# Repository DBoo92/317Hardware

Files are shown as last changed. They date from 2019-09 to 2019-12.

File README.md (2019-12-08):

# 317Hardware

## Table of Contents

- [Introduction](#introduction)
- [Bill of Materials](#bill-of-materials)
  * [Parts list](#parts-list)
  * [Custom Parts](#custom-parts)
  * [Tools List](#tools-list)
- [Time Commitment](#time-commitment)
- [PCB/Soldering](#pcbsoldering)
  * [ADS1115 soldering](#ads1115-soldering)
  * [PCB soldering](#pcb-soldering)
  * [Motor soldering](#motor-soldering)
  * [Sensor soldering](#sensor-soldering)
- [Mechanical Assembly](#mechanical-assembly)
  * [ADS1115 risers](#ads1115-risers)
  * [PCB risers](#pcb-risers)
  * [Thread acrylic](#thread-acrylic)
  * [Mount Pi](#mount-pi)
  * [Mount motor](#mount-motor)
  * [Install case fan](#install-case-fan)
  * [Assemble case](#assemble-case)
  * [Plug in connectors](#plug-in-connectors)
  * [Water lines](#water-lines)
  * [Spray nozzle](#spray-nozzle)
- [Power Up](#power-up)
  * [Load OS](#load-os)
  * [Import libraries](#import-libraries)
- [Unit Testing](#unit-testing)
  * [Sensor test](#sensor-test)
  * [Water switch test](#water-switch-test)
  * [Motor test](#motor-test)
  * [Full system test](#full-system-test)
- [Production Testing](#production-testing)
- [Conclusion](#conclusion)

## Introduction

Welcome to my CENG 317 hardware project page. The aim of this project is to create a system for monitoring greenhouse conditions using a Broadcom development platform and various sensors/effectors. Here is a diagram of the proposed systemm:

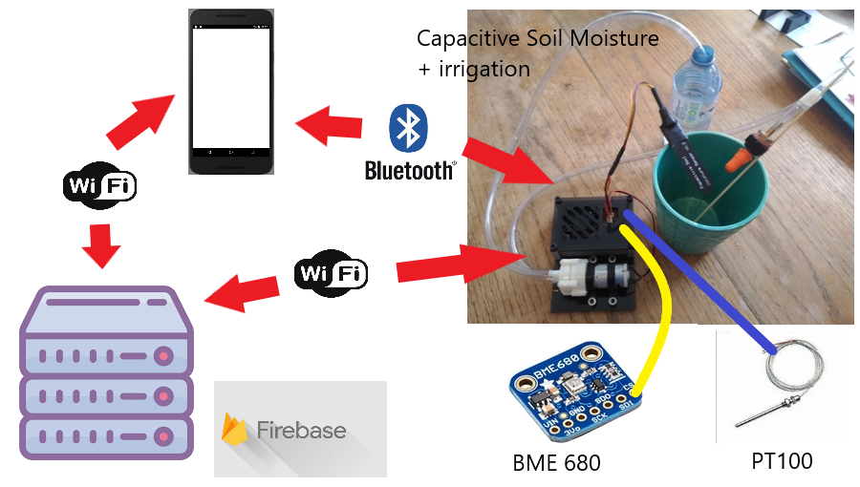
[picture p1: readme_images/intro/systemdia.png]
Systemdiagram


The system consists of a Raspberry Pi which takes readings from various sensors and places them into a Firebase database via WiFi. If these readings are outside of certain ranges/thresholds the device will activate a certain effector to adjust the environment/conditions. All of this data will be viewable from within our app which will connect to the database via WiFi. The app will also be able to control/turn on the various effectors through Bluetooth.

The BME 680 and PT100 sensors are being covered by my group members, Ryan and Aiden respectively.The app is covered in a different course, CENG 319 - [GreenSense App](https://github.com/Aidenbolos/Green-Sense). These build instructions will focus solely on the capacitive soil moisture platform (seen in the system diagram above and the diagram below).

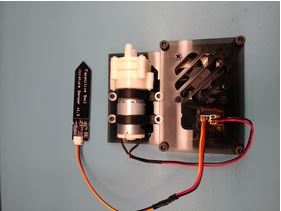
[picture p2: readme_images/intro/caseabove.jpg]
soilmoisture


This project features a capacitive soil moisture sensor for monitoring soil conditions, a pump/irrigation system for watering the plant/soil, and a watering level switch for selecting the amount of water to be dispersed to the plant. 

## Bill of Materials

### Parts List:

| Part/Material | Part Number | Supplier | Qty | Approx. Cost |
|---|---|---|:---:|---:|
| Raspberry Pi 4 starter kit <br> (includes power supply, HMDI, <br> SD card, and card reader) | 99467 | CanaKit (Amazon) | 1 | $134.99 |
| Capacitive Soil Moisture sensor | EK1940 | Gikfun (Amazon) | 1 | $8.48 |
| Mini Diaphragm Pump | EK1856C | Gikfun (Amazon) | 1 | $11.67 |
| ADS1115 (or ADS1015) | 4260474032037 | Universal Solder (Amazon) | 1 | $7.89 |
| 1K ohm resistor | | Electronics store | 3 | $0.30 |
| PN2222A transistor | | Electronics store | 1 | $0.25 |
| IN4001 diode | | Electronics store | 1 | $0.15 |
| 1P3T switch | SMC-549-1 | Sayal Electronics | 1 | $1.50 |
| 2.1mm DC power jack | GAK-1973E-2 | Sayal Electronics | 1 | $0.80 |
| 6v - 12v power supply (2.1mm plug) | | Electronics store | 1 | $9.95 |
| 50mm case fan (with screws) | 8880205 | Princess Auto | 1 | $1.99 |
| 20 pin GPIO header (single row) | | Electronics store | 1 | $0.50 |
| 3 pin Molex connectors (female) | 37-603-5 | Mode Electronics (Sayal Electronics) | 2 | $1.00 |
| 3 pin Molex header (male) | 37-6203-5 | Mode Electronics (Sayal Electronics) | 2 | $1.00 |
| 22 AWG solid wire | | Electronics store | 1 ft | $0.50 |
| 1/8" heatshrink | | Electronics store | 1 ft | $0.40 |
| 63/37 solder (small roll) | 4880-18G | MG Chemicals (Sayal Electronics) | 18g | $3.95 |
| Cone spray nozzle (3/8" thread) | SG-4200TIP-CSK| Valley Industries (Princess Auto) | 1 | $6.49 |
| 1/4" barbed to 3/8" NPT fitting | 903-41161001  | Sioux Chief (Home Depot) | 1 | $3.25 |
| Clear vinyl tube 1/4" ID | | Hardware store | 4 ft | $2.00 |
| M5 x 0.8 x 40mm socket head screw | | Bolts Plus | 4 | $2.80 |
| M3 x 0.5 x 16mm socket head screw | | Bolts Plus | 4 | $1.60 |
| M2.5 x 0.45 x 10mm button head screw  | | Bolts Plus | 4 | $1.20 |
| M3 x 0.5 nuts | | Bolts Plus | 4 | $0.40 |
| M2.5 x 0.45 nuts | | Bolts Plus | 2 | $0.10 |
| M3 washers | | Bolts Plus | 20 | $1.00 |
| 10mm PCB risers (with nuts/screws) | | Hardware store | 4 | $0.80 |
| 12" x 12" x 1/8" acrylic | | Hardware store | 1 | $10.00 |

### Custom Parts:

| Part | Source file | Approx. Cost |
|---|---|---:|
| PCB manufacturing | [PCB gerber files](https://github.com/DBoo92/317Hardware/blob/master/electronics/SoilMoisture_Gerber.zip) | $20.00 |
| 3D printing | [3D .stl file](https://github.com/DBoo92/317Hardware/blob/master/mechanical/ProjectBoxMiddleRPI.stl)| $15.00 |
| Acrylic laser cutting | [Acrylic Top cut file](https://github.com/DBoo92/317Hardware/blob/master/mechanical/CaseTop.cdr) <br> [Acrylic Bottom cut file](https://github.com/DBoo92/317Hardware/blob/master/mechanical/CaseBottom.cdr) | $10.00 |

> Tip 1: If you haven't already ordered/received the custom parts above, please find a PCB manufacturer, 3D print shop, and a laser cutting shop. Use the source files above and have these parts made before beginning your project.

### Tools List:

| Tool                       | 
|----------------------------|
| HDMI monitor/TV            |
| USB mouse and keyboard     |
| Soldering iron             |
| Wire strippers             |
| Diagonal cutting pliers    |
| Heat gun (or blow dryer)   |
| Digital Multimeter         |
| M5 x 0.8 tap + handle      |
| Small square file          |
| 4mm allen key              |
| 2.5mm allen key            |
| 1.5mm allen key            |
| Philips #2 screwdriver     |
| X-Acto knife               |

## Time Commitment

Time required to complete this project is approximately: **12 - 16 hours** (continuous work), or 2 work days. This varies depending on skill level.

It is best to approach this project with mild/moderate experience in electronics and circuits, tools and assembly, and computers. However, my aim is to make this guide thorough enough for people of all experience levels.

## PCB/Soldering

Follow the steps below to assemble/solder your PCB.

> Hint: If you do not have prior soldering experience, I recommended reading [this](https://www.makerspaces.com/how-to-solder/) website and watching their demonstration video.

Before beginning please ensure you have an adequate workspace, the appropriate tools, and that everything is clean and tidy. The appropriate safety equipment is outlined in the website above.

### ADS1115 soldering

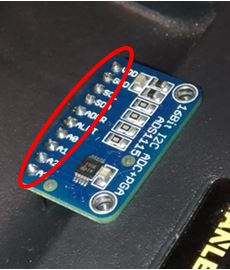
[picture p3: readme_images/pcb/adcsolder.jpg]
ADSsolder Fig 4.1: ADS1115 solder points


Place the 10 pin header through the ADS1115 with the short side of pins going through the holes. Ensure that the pins are at a 90 degree angle with the circuit coard. Solder each pin as circled in red above. Allow time to cool between each solder joint.

### PCB soldering

#### 1. Vias

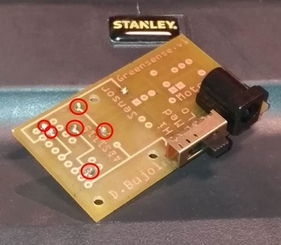
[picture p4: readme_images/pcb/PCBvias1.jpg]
PCBvias1 Fig 4.2: Via solder points (top)
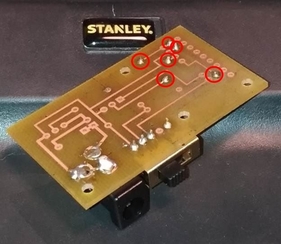
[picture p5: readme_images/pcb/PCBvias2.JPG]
PCBvias2 Fig. 4.3: Via solder points (bottom)
 

Begin by cutting six 2" lengths of your solid core wire and stripping them completely. Place a piece of wire through one of the holes circled in red and solder one side of it. Once the solder joint has cooled, flip the PCB over and solder the other side of the same wire. Using the diagonal cutters, carefully cut off the excess wire on either side down at the tip of the solder joint. Repeat this process for the other 5 holes circled in red.

#### 2. DC Jack and 1P3T Switch

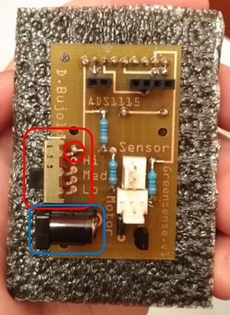
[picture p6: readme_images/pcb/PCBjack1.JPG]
PCBjack1 Fig 4.4: Jack and switch placement
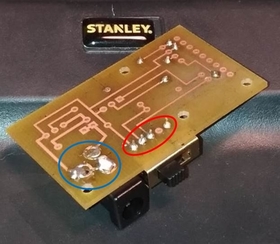
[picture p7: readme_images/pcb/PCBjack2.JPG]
PCBjack2 Fig 4.5: Jack and switch solder points
 

Place the DC jack (first image circled in blue) into its mounting holes on the PCB. Ensure that the jack is sitting on top of the board, facing out the side, and its pins/tabs stick out the bottom. Bend the 3 tabs down towards the PCB to help hold the jack in place and to allow for a better solder connection. Solder each tab individually on the bottom of the board (second image circled in clue). Allow time to cool in between each pin (to avoid melting the plastic).

Place the 1P3T switch (first image circled in red) into its mounting holes on the PCB. Ensure that the switch is sitting on top of the board, facing out the side, and its pins stick out the bottom. Bend the pins slightly to help hold the switch in place. Solder each pin individually on the bottom of the board (second image circled in red). After this is done solder just the far left hand pin from the top as well (first image interior red circle). One hole will remain empty as seen in the second image.

#### 3. Resistors

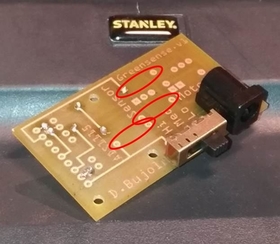
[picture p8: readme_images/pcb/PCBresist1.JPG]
PCBresist1 Fig 4.6: Resistor holes
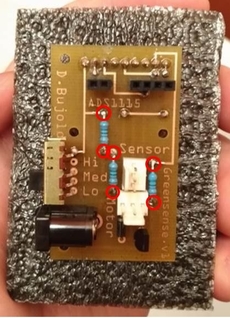
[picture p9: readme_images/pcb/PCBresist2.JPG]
PCBresist2 Fig 4.7: Resistor solder points (top)
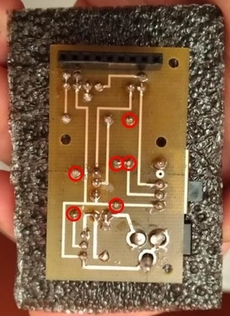
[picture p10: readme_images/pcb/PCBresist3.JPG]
PCBresist3 Fig 4.8: Resistor solder points (bottom)
  

Bend the legs on your 1k ohm resistors so each resistor aligns with a pair of holes (first image circled in red). Place the first resistor into its mounting holes from the top of the board and bend the legs from underneath to hold it in place. Solder both the top and bottom holes (second and third image circled in red). Allow time to cool between solder joints to prevent overheating the resistor. Do this for the other 2 resistors.

#### 4. Diode

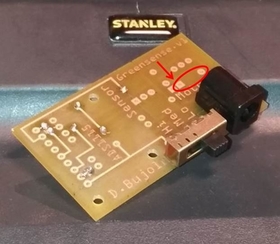
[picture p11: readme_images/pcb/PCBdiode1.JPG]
PCBdiode1 Fig 4.9: Diode holes
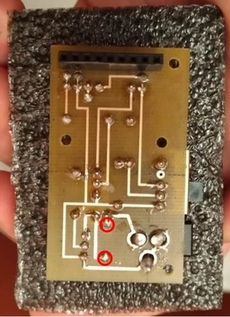
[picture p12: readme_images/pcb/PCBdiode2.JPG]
PCBdiode2 Fig 4.10: Diode solder points (bottom)
 

Bend the legs on your diode so it aligns with its pair of holes (first image circled in red). 

> Tip 2: The silver line on your diode MUST face the square pad on the board (red arrow pointing to it).

Place the diode into its mounting holes from the top of the board and bend the legs from underneath to hold it in place. Solder the diode from underneath the board. Allow time to cool between solder joints to prevent damaging the diode.

#### 5. Transistor

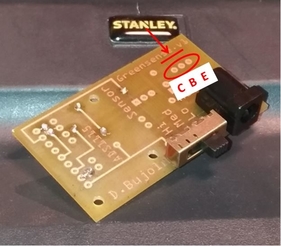
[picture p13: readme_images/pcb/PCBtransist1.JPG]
PCBtransist1 Fig 4.11: Transistor holes
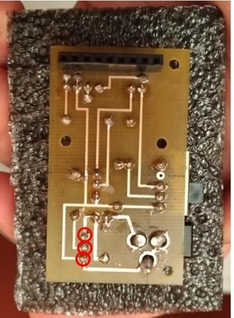
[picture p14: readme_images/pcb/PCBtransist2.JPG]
PCBtransist2 Fig 4.12: Transistor solder points (bottom)
 

Place the transistor into its mounting holes from the top of the board (first image circled in red).

> Tip 3: The flat side on the transistor body MUST face the flat red line in the diagram. However, if you are using a different transistor/package please refer to its data sheet to determine its orientation (collector, base, and emitter are labelled in the diagram).

Bend the pins on the transistor from underneath to help hold it in place. Solder the transistor pins from underneath the board (second image circled in red). It is very important you allow time to cool between each solder joint as transistors are very sensistive to heat.

#### 6. Molex Connectors

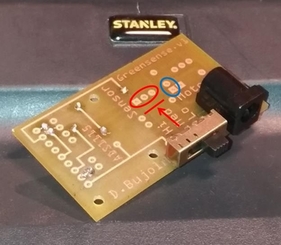
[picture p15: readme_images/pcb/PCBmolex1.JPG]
PCBmolex1 Fig 4.13: Molex holes
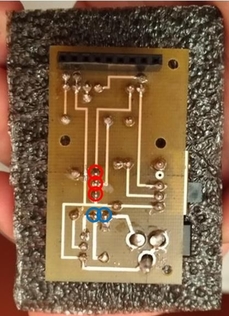
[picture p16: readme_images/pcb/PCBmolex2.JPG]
PCBmolex2 Fig 4.14: Molex solder points (bottom)
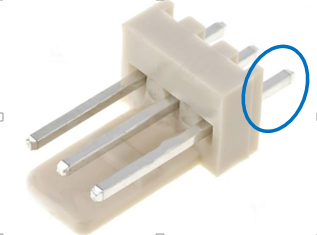
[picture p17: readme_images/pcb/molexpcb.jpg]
PCBmolex3 Fig 4.15: Unused molex pin
  

Place the soil sensor molex connector (circled in red) into its mounting holes from the top of the board.

> Tip 4: The plastic "tab" on the molex connector should face the flat red line in the diagram.

Bend the pins from underneath to hold it in place. Solder each pin from underneath the board (second image circled in red).

For the motor molex connector, cut off or bend flat the bottom pin (third image circled in blue) as it will interfere with mounting and is unused. Place the connector into its mounting holes from the top of the board (first image circled in blue). Solder the two pins from underneath the board (second image circled in blue).

#### 7. ADC and Pi Headers

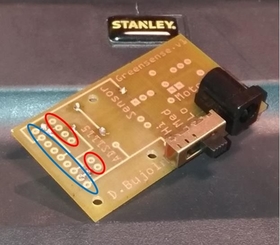
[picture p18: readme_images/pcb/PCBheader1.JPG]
PCBheader1 Fig 4.16: Header holes
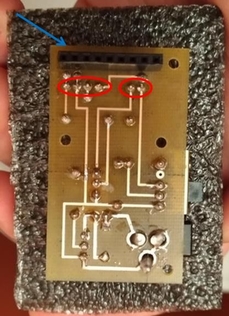
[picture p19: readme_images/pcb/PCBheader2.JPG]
PCBheader2 Fig 4.17: Header solder points (bottom)
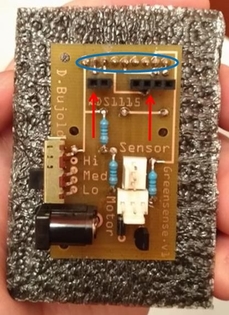
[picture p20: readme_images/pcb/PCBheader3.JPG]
PCBheader3 Fig 4.18: Header solder points (top)
  

If you haven't already, now is the time to cut your headers to size. You will need one 2 pin, one 4 pin, and one 9 pin header. Carefully use the X-Acto knife to cut your headers to the desired size.

Push the 4 pin header onto the Vcc, Gnd, SDA, and SCL pins of the ADS1115. Push the 2 pin header onto the A0 and A1 pins of the ADS1115. Place the headers into their mounting holes from the top of the PCB (first image circled in red) and ensure that the pins stick out the bottom. Flip the PCB over so it is now resting on the ADS1115. Prop up the PCB so it is parallel and square with the ADS1115. Solder the the header pins on the bottom side of the board (second image circled in red).

Push the 9 pin header onto your Raspberry Pi so it sits on pins 1, 3, 5, 7, 9, 11, 13, 15, and 17. Now place the entire PCB (bottom down) onto the 9 pin header (the pins should stick out the top of the PCB - first image circled in blue). Prop up the PCB so it is parallel and square with the Raspberry Pi. Solder the two outermost pins from the top side of the board (third image circled in blue). Now remove the PCB from the Pi with the 9 pin header attached. Finish soldering the other 7 pins from the top side of the board.

#### 8. PCB notch

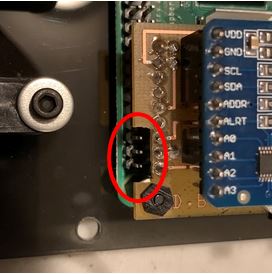
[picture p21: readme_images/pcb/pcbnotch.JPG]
PCBnotch Fig 5.11: Notch for fan power


Use the small square file to cut a notch in the PCB beside the first 3 header pins. Copy the notch in the image above. This will allow us access to the Pi's 5v and Gnd to plug in the case fan.

Now that you have completed the PCB, it is advised to run a couple quick tests:

> Test 1: It is recommended to do continuity tests on side-by-side solder joints or any connections that look close to each other/touching. This is a precaution to help ensure there are no shorts between solder joints.

> Test 2: Use a jumper wire to connect Vcc and Gnd together on the PCB sensor circuit (connect the pins in the header). Then, using a DMM set to ohms, measure resistance between Gnd and A0 on your ADC. You should see a reading between a few hundred thousand ohms and a few million ohms. If you see this reading it indicates your sensor circuit is wired correctly.

### Motor soldering

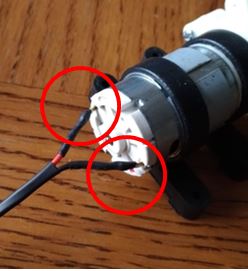
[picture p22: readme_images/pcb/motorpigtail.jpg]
motorsolder Fig 4.19: Motor terminal wires


Cut two pieces of 22 AWG solid wire approximately 8" long and strip 1/4" off each end. Wrap the end of one wire onto one of the motor terminals. Solder this connection. Cut off a 2" piece of heatshrink and slide it down the wire and over the connection. Use the heat gun to heat up the tubing and shrink it. Repeat this process for the second wire and the second motor terminal.

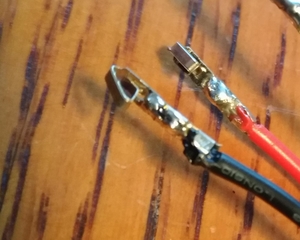
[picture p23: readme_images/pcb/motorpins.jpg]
motorwires Fig 4.20: Motor wires molex pins
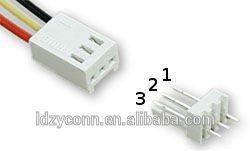
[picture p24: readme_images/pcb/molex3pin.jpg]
motormolex Fig 4.21: Molex pin numbers
 

Using the wire strippers crimp a molex pin onto the open end of each motor wire (shown in the first image). Apply a small amount of solder to the crimp connection to strengthen it. Once the solder has cooled, insert the pins into holes 1 and 2 as labelled in the second picture (doesn't matter which pin goes in which hole).

### Sensor soldering

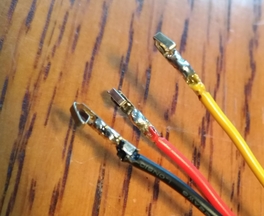
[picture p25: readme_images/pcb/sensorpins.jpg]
sensorwires Fig 4.22: Soil sensor molex pins
 sensormolex Fig 4.23: Molex pin numbers

Cut the stock connector off the soil sensor using the diagonal cutters. Make your cut close to the existing connector so the wires stay long. Strip about 1/4" off the end of each wire. Crimp a molex pin on the open end of each wire (shown in first image) using the wire strippers. Apply a small amount of solder to the crimp connection to strengthen it. Once the solder has cooled, insert the Aout pin into hole 1, Vcc pin into hole 2, and Gnd pin into hole 3 (as labelled in the second picture).

> Tip 5: Make sure the pins go into the appropriate connector hole otherwise it may damage the sensor/circuit.

You are now ready for mechanical assembly.

## Mechanical Assembly

### ADS1115 risers

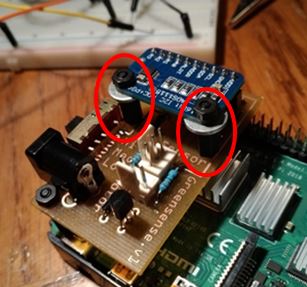
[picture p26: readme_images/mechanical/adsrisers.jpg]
ADSrisers Fig 5.1: ADS1115 risers


Start by inserting a 10mm riser in each mounting hole of the ADS1115 with a 3mm washer underneath it (as shown in the picture). Fasten them by threading a nut on the end of the riser and tightening it. Then from the bottom side of the PCB thread a screw into the riser through the 2 mounting holes and tighten them. Careful not to overtighten anything as the risers are only plastic.

### PCB risers

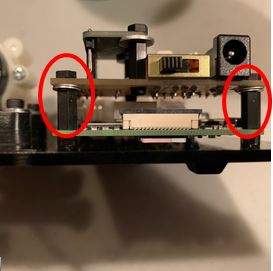
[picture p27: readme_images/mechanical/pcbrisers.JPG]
PCBrisers Fig 5.2: PCB risers


Next insert a 10mm riser into each outer mounting hole on the PCB with a 3mm washer underneath it (as shown in the picture). Fastern them by threading a nut onto the end of the riser and tightening it. Careful not to overtighten as the risers are only plastic.

Now that the ADC is mounted to the PCB and the PCB has its own risers; you are ready to install it onto the Raspberry Pi. Place the PCB onto the Raspberry Pi by lining up the 9 pin header with pins 1, 3, 5, 7, 9, 11, 13, 15, and 17 on the Pi. Press straight down gently on the header to fully seat the PCB onto the Pi.

### Thread acrylic

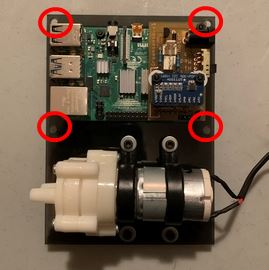
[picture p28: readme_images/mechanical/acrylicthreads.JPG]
acrylicthreads Fig 5.3: Acrylic holes to tap


Before mounting anything to the bottom layer of acrylic, use the M5 x 0.8 tap + handle to tap/thread these 4 holes (outlined in red). 

> Hint: If you haven't used a tap before, follow the instructions on [this](https://disher.com/2016/11/08/whats-tap-hand-taps-beginners/) website.

### Mount Pi

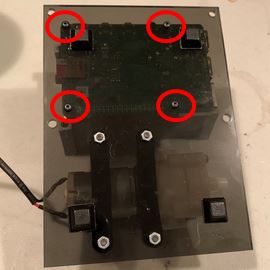
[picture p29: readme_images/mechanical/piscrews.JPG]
Piscrews Fig 5.4: Pi mounting screws
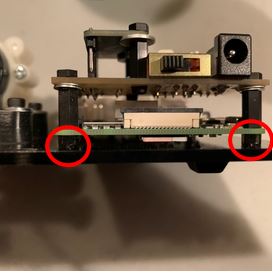
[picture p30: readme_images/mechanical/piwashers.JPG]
Piwashers Fig 5.5: Pi spacers/washers
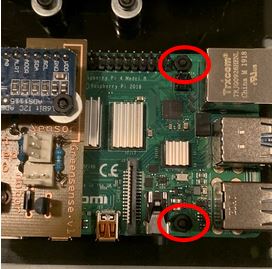
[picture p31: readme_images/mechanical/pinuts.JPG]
Pinuts Fig 5.6: Pi mounting nuts
  

Place an M2.5 x 10mm screw through each of the Pi mounting holes in the acrylic (first image circled in red). Lie the acrylic bottom down with the bolt heads against the table (the bolt threads should be facing upward). Place three 3mm washers onto each bolt on top of the acrylic (similar to the second image). Then line up the Pi over the bolts and lower it on to them (audio/video ports should face outside edge). Thread a M2.5 nut onto the two bolts closest to the ethernet/USB ports and tighten them (third image). Carefully prop the unit up on its side, ensuring the other 2 mounting bolts stay in their holes (as they are not threaded in yet). Use the 1.5mm allen key to tighten up the other 2 mounting bolts from underneath the acrylic (don't overtighten as they are threading into the plastic risers).

### Mount motor

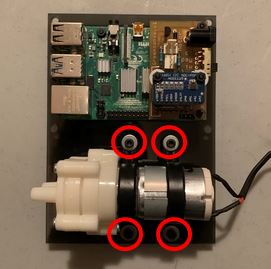
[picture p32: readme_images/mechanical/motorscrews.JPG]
motorscrews Fig 5.7: Motor mounting screws
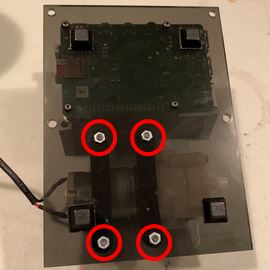
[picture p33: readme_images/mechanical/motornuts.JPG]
motornuts Fig 5.8: Motor mounting nuts
 

Install the included rubber mounts onto the motor body. Place the motor onto the acrylic base. Insert a M3 x 0.5 x 16mm screw with a 3mm washer into each mounting hole (first image circled in red). Then thread a nut onto the bottom of each screw from underneath (second image circled in red). Hold the nut with you fingers while using the 2.5mm allen key to tighten them. The motor mounts are only rubber so do not overtighten/compress the rubber.

### Install case fan

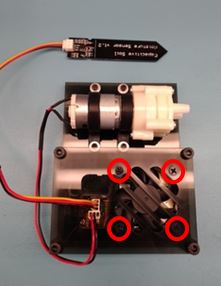
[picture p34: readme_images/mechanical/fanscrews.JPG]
fanscrews Fig 5.9: Case fan screws


Place the fan against acrylic top cover with the "cage" part of the fan facing down (this will ensure air is pulled in). Then use the Philips #2 screwdriver thread the fan screws into the fan (circled in red). Lightly tighten the screws but do not overtighten as the acrylic may crack.

### Assemble case

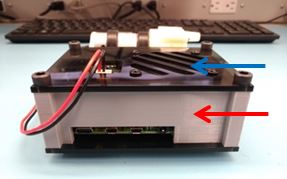
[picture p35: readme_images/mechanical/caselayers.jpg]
caselayers Fig 5.10: Layers of the case
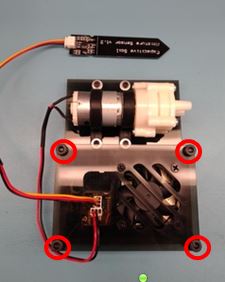
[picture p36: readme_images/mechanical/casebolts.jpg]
casebolts Fig 5.12: Case fastening bolts
 PCBnotch Fig 5.11: Notch for fan power 

Assemble the case by fitting the 3D printed middle section (first image red arrow) over the Pi and onto the acrylic base. Then plug the fan connector into 5v and Ground on the Pi header (where the notch was cut earlier - second image circled in red). Now place the acrylic top (first image blue arrow) onto the 3D printed middle section. Finally, insert the four M5 x 0.8 x 40mm bolts through all three layers and thread them into the bottom layer (third image circled in red). Tighten these bolts with the 4mm allen key (careful not to overtighten).

### Plug in connectors

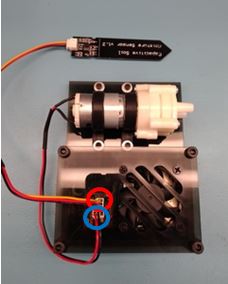
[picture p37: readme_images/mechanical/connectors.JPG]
connectors Fig 5.13: Molex plug in location


Now that the case is assembled we can add the sensor and effector. Plug the 3 pin soil sensor into the center connector on the PCB (circled in red). Then plug the motor connector into the remaining connector on the PCB (circled in blue).

### Water lines

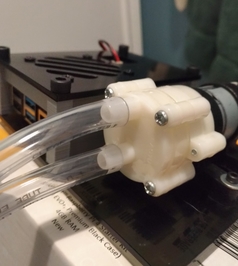
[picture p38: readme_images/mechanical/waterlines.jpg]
waterlines Fig 5.14: Water line attachment


Using the diagonal cutters, cut the clear vinyl tubing into 2 equal length pieces (around 2 ft each). Push the end of a tube onto each water pump barb as shown in the image above.

### Spray nozzle

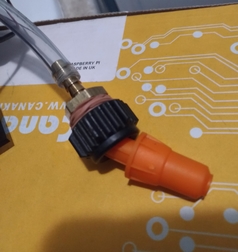
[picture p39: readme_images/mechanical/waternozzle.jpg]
waternozzle Fig 5.15: Spray nozzle setup


Thread the 1/4" barb to 3/8" NPT brass fitting into the spray nozzle threads. Tighten these together firmly to prevent leaks. See above image for reference.

Look on the face of the water pump (where the tubes connect) and note which tube is labelled "IN" and which is "OUT". Then push the barbed end of the nozzle into the open end of the "OUT" tube (as shown in the image above).

You are now ready to power up.

## Power Up

> Tip 6: If you haven't already, please complete the 2 tests listed at the bottom of the PCB soldering section. These will help ensure that no damage is done to your Pi during initial power up.

### Load OS

1. Unfortunately the OS file is too large to post on Github. However, the link below will take you to the Raspberry Pi download page where you can get it. There you can download the OS as either a torrent or a zip file. For this project it is recommended to download the full "Raspbian Buster with desktop and recommended software". You will need at least an 8GB SD card for this.

[Download Raspbian OS](https://www.raspberrypi.org/downloads/raspbian/)

2. Once downloaded, follow the link below for instructions on flashing the OS onto your SD card.

[Install Raspbian OS](https://www.raspberrypi.org/documentation/installation/installing-images/README.md)

3. Finally, follow the link below for help with the intital power up/configuration setup:

[Configure Raspbian](https://projects.raspberrypi.org/en/projects/raspberry-pi-setting-up/4)

4. The Pi starter kit comes with an HDMI cable, so for your initial tests you will be connecting it to an HDMI monitor. However, in the future you are recommended to download VNC Viewer to connect remotely via WiFi or ethernet.

[Download VNC Viewer](https://www.realvnc.com/en/connect/download/viewer/)

5. Use the guide below to help you setup/use VNC Viewer and connect to your Pi.

[Setup VNC Viewer](https://magpi.raspberrypi.org/articles/vnc-raspberry-pi)

### Import libraries

Now that the Pi is setup and running you will need to import this library to access the readings from the ADS1115.

Open the terminal and run the following commands one at a time. You may see some text appear between each command, allow it to finish before inputting the next command.

```sh
sudo apt-get update
sudo apt-get install build-essential python-dev python-smbus git
cd ~
git clone https://github.com/adafruit/Adafruit_Python_ADS1x15.git
cd Adafruit_Python_ADS1x15
sudo python setup.py install
```

You now have the necessary libraries and some sample code to work with.

## Unit Testing

I suggest testing the sensor and watering level switch first without the motor functionality. This way it is easier to troubleshoot if you run into problems.

### Sensor test

Now that everything is assembled and the software is installed you are ready to test the sensor. The sensor should be connected to the PCB at this point and you should have a glass of water nearby to simulate soil moisture.

Power up your Pi and open a terminal session. Enter the following command to navigate to the Adafruit example code you downloaded earlier:

```sh
cd ~/Adafruit_Python_ADS1x15/examples
```

Now that you are in the examples folder, run this command:

```sh
nano simpletest.py
```

> Tip 7: Use CTRL-c to stop the program when you are done.

The program should start up in the terminal. You will see the readings of the 4 ADS1115 channels displayed in a table. See the picture below as an example:

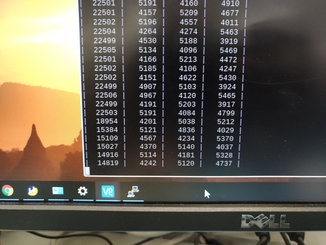
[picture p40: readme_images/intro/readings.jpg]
readings Fig 7.1: Test readings


The soil sensor values are shown in the first column. In dry air the sensor should read around 24,000. Test the senor by placing it into the glass of water. You should see these readings drop down below 15,000. Repeat this a few times to ensure things are working well.

### Water switch test

The watering level switch values are shown in the second column. Test the switch by flipping it between its 3 positions. You should see the readings change between low (under 1000), medium (around 15000), and high (over 24000). Again, repeat this a few times for verification. You may stop the program now.

Once you have confirmed that these two are working correctly you may now test the motor.

### Motor test

The motor should be connected to the PCB and the water hoses connected to the motor. Plug the 6 - 12v power supply into the wall and plug the 2.1mm plug into the DC jack on the PCB. Place the "IN" hose into a cup of water and the "OUT" hose into an empty cup. Unscrew and remove the top cover from the project case and disconnect the fan for now. Using a wire with alligator clips on either end, clip one end to the Pi 5v output (where the fan was connected). Clip the other end onto the middle leg (Base) of the transistor (careful not to touch the other legs). The motor/pump should now turn on. Check to make sure the pump is working correctly and you are getting a steady mist/stream out of the spray nozzle. Once you are done - remove the alligator clips, replace the fan connector, and reinstall the top cover.

If all three components are working correctly you are ready to proceed to the full system test.

### Full system test

Now you are ready to test the complete system. Ensure that the sensor and motor are connected to the PCB, and the water hoses are connected to the motor. Plug the 6 - 12v power supply into the wall and insert the 2.1mm plug into the DC jack on the PCB. Go outside and fill a pot/cup with soil. Place the soil sensor into the soil (not past the warning line), point the sprayer nozzle toward the soil (but away from the sensor), and put the "IN" hose in a bottle of water.

Open the Pi's web browser and download the modified program from here - [readingsupdated.py](https://github.com/DBoo92/317Hardware/blob/master/software/readingsupdated.py). Make sure you save it into the downloads folder.

Open a terminal session. Then move the downloaded file to the Adafruit examples folder (for the convenience of keeping your code in the same folder) using this command:

```sh
cp ~/Downloads/readingsupdated.py ~/Adafruit_Python_ADS1x15/examples
```

Use this command again to navigate to the example code folder:

```sh
cd ~/Adafruit_Python_ADS1x15/examples
```

And use this command to run the new program:

```sh
nano readingsupdated.py
```

Remember that the sensor is in the (hopefully) moist soil, so the water should not turn on. If the water does turn on initially, it just means the soil readings are dry. If the water doesn't turn on, you may wait for the moisture levels to drop to turn the pump on (which will take a while). Or you can test the pump by simply removing the sensor from the soil. This will expose the sensor to dry air, which should then trigger the pump to turn on. See the video below as an example:

Fully functioning system:
ReadingsVideo (https://youtu.be/7LPlyvlskEI "CENG 317 soil readings")

Also, test out the different positions on the watering level switch. The different positions should change how long the pump stays on for. This directly affects how much water the plant gets.

Test these variations out a few times to ensure everything is working. You can even leave it running for a few hours and monitor it. As long as both channels are reading fine and the water system turns on when the threshold is crossed, all is well. 

**If you've ran all these tests and everything is working as described - then congratulations! You have succesfully completed the soil moisture sensor project!**

## Production Testing

There are a couple steps to my production testing methods.

1. Bench test jig - run on every PCB

This consists of a test jig to test the PCB for resistance. The PCB gets plugged into a jig which has a built in jumper between the Vcc and Gnd on the soil sensor circuit. A soil sensor (taken from the line) and plugged into its header on the PCB. Then using a DMM on the test bench, check resistance between Gnd and A0. This value should read between a few hundred thousand ohms to a few million ohms on success.

The jig would also feature a 12v 2.1mm plug to insert into the DC jack. The jig will apply voltage to the transistor "Base" header pin to turn it on. Using the DMM, voltage would be checked across the motor header pins on the PCB. This value would read approx. 12v on success. We use a 12v power supply to see if the motor/circuit can withstand its rated voltage.

This process would end with a visual check of all components on the PCB, all solder joints, and the soil sensor. If it passes these tests, the soil sensor and the PCB are kept as a pair and returned to production for packaging. If not, we would try another soil sensor to see if the problem was the sensor or the PCB. If it still fails, then they are used to investigate where the failure occured and why.

This gives us good quality control and eliminates a lot of issues from getting out the door.

Once this bench test returns a reasonable success rate, we could cut back to testing every 5th PCB on the line.

2. Full test jig - every 20th PCB

This consists of a complete test jig - Raspberry Pi with pre-installed OS and needed programs, water lines + sprayer, and 12v power supply with 2.1mm plug. We would install the PCB onto the Pi, then we would take an ADS1115, soil sensor, and motor from the production line and connect them. Then all other peripherals would be connected (but no fastening things together). The full readingsupdated.py program would be run to see if the system functions as it should (as outlined in "Full system test" above). We use a 12v power supply to see if the motor/circuit can withstand its rated voltage. We would test the extremes of dry air vs. moisture to see the sensor's range.

This process would end with a visual check of all components on the PCB, all solder joints, the ADS1115, the soil sensor, and the motor. If it passes these tests, the soil sensor, motor, ADS1115, and the PCB are kept as a unit and returned to production for packaging. If not, we would try to narrow down the problem to the PCB, ADS1115, soil sensor, or the motor by switching them out for others. If it still fails, then they are used for futher investigation into where the failure occured and why.

This enables us to test the entire system and ensure that all features are functioning consistently. However this process is somewhat labour intense, which is why it is only done to every 20th unit.

This gives us fairly good quality control, while also balancing cost and not testing units so frequently.

## Conclusion

Thank you for taking the time to read and review my project. I hope it was informative and helpful for you. Please feel free to try it out yourself.

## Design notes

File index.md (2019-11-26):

Capstone Project - Greenhouse Monitoring System
-----
-----
### November 26, 2019 - Presentation Due

[PowerPoint presentation](https://github.com/DBoo92/317Hardware/blob/master/presentation/317Presentation.pptx) slides have been posted in the presentation folder.

I will be presenting this next week.

-----

### November 23, 2019 - Programming pdate

I updated my sample Python program to include functionality for the watering level switch and irrigation/motor system. You can find the updated program under software/readingsupdated.py

Here is the code fragment:
```python
 # Print the ADC values.
    print('| {0:>6} | {1:>6} | {2:>6} | {3:>6} |'.format(*values))

    # Declare variable for watering level switch
    water_lvl = 0

    # Declare variable for moisture reference value
    ref = 13000

    # Set watering level
    if (values[1] < 1000):
	water_lvl = 0.5
    elif (values[1] > 12000 and values[1] < 14000):
	water_lvl = 1.5
    elif (values[1] > 24000):
	water_lvl = 3
    else:
	water_lvl = 1

    # Turn on motor/watering system if soil moisture is too low
    if (values[0] > ref):
        GPIO.output(22,GPIO.HIGH)
        # Turn motor on for water_lvl seconds
	   time.sleep(water_lvl)
        GPIO.output(22,GPIO.LOW)
        # sleep to allow water absorbtion before recheck
	   time.sleep(10)

    # Pause for 2 seconds.
    time.sleep(2)
```

Video of the fully functioning system (watering level is set to "medium" or 1.5 seconds):
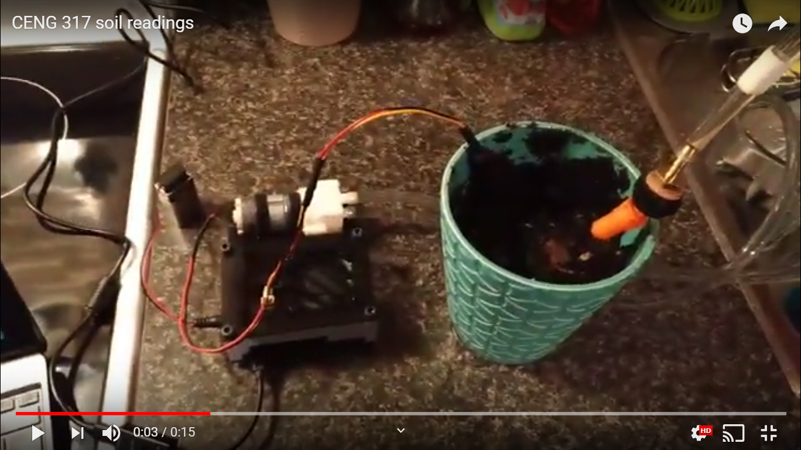
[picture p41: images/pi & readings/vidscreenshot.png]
ReadingsVideo (https://youtu.be/7LPlyvlskEI "CENG 317 soil readings")


-----

### November 22, 2019 - Hardware Update

Heat shrink to protect sensor electronics:  
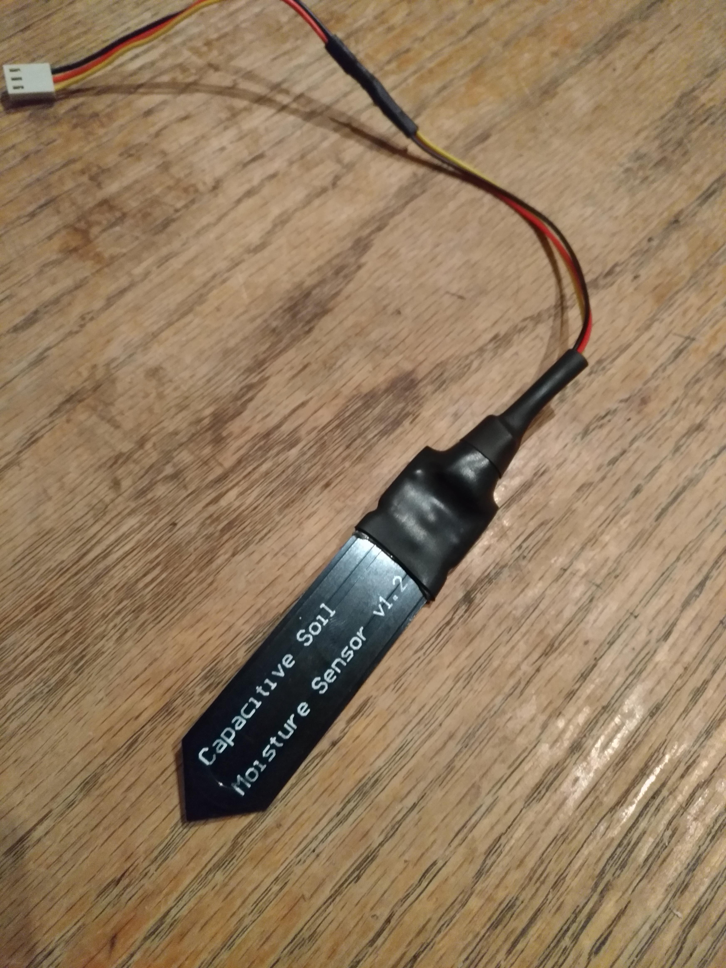
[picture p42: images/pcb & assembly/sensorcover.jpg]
sensorcover


-----

### November 19, 2019 - Enclosure Due

Completed enclosure assembled:  
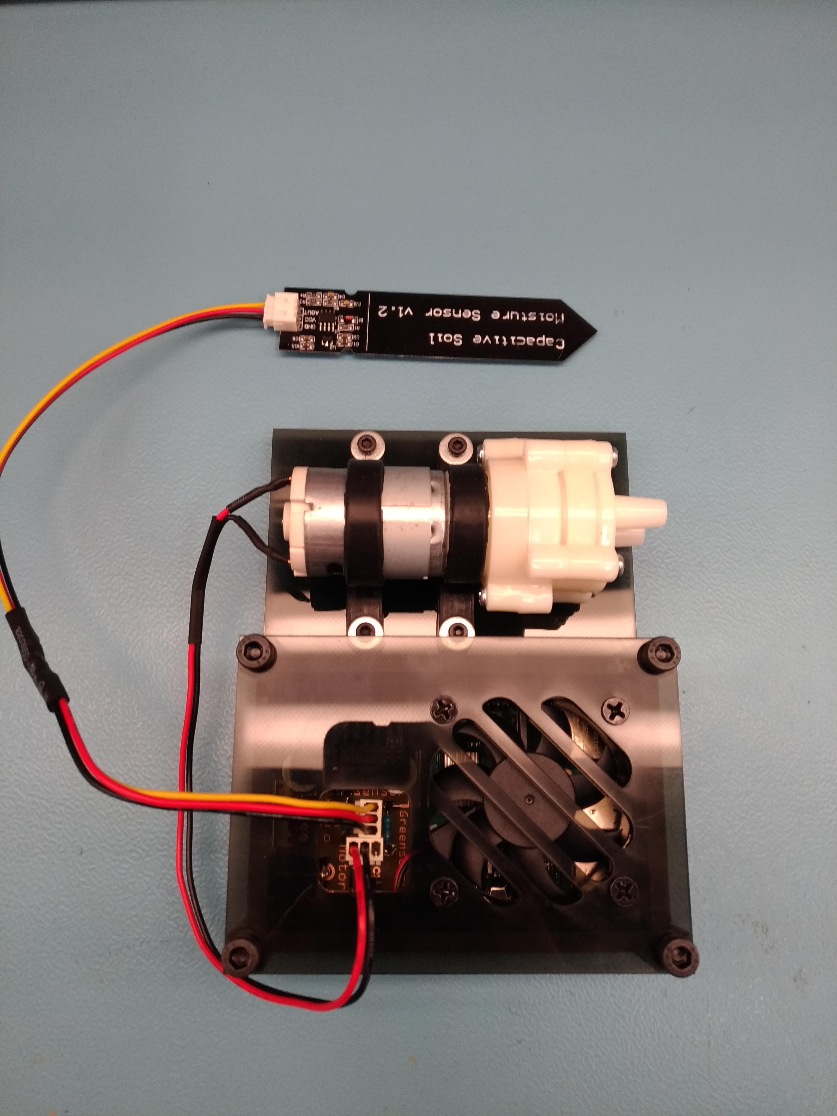
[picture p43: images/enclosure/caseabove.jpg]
case1


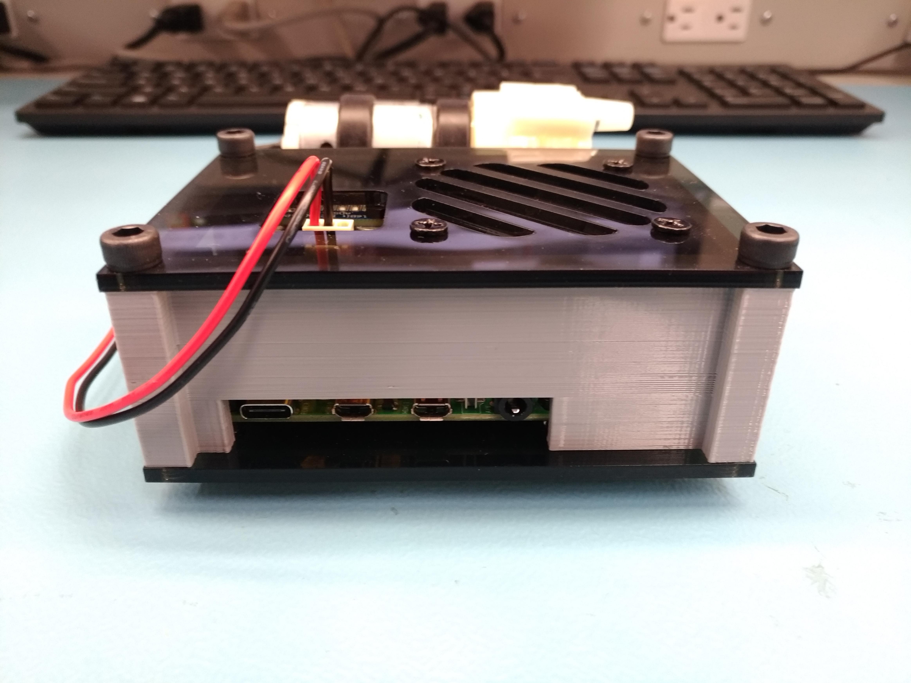
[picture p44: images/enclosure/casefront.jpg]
case2


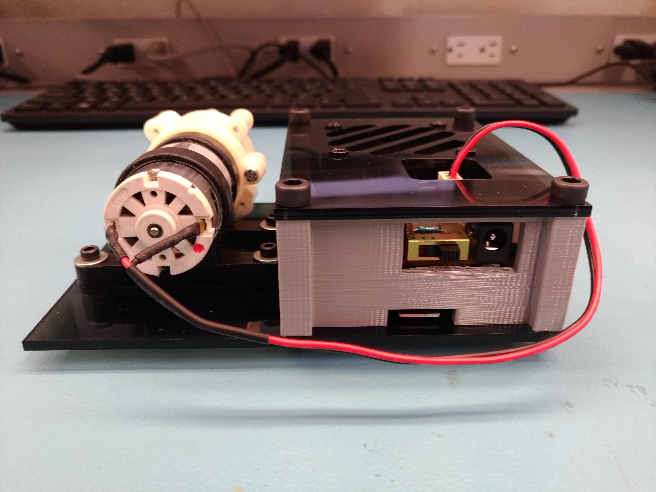
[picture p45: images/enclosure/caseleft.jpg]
case3


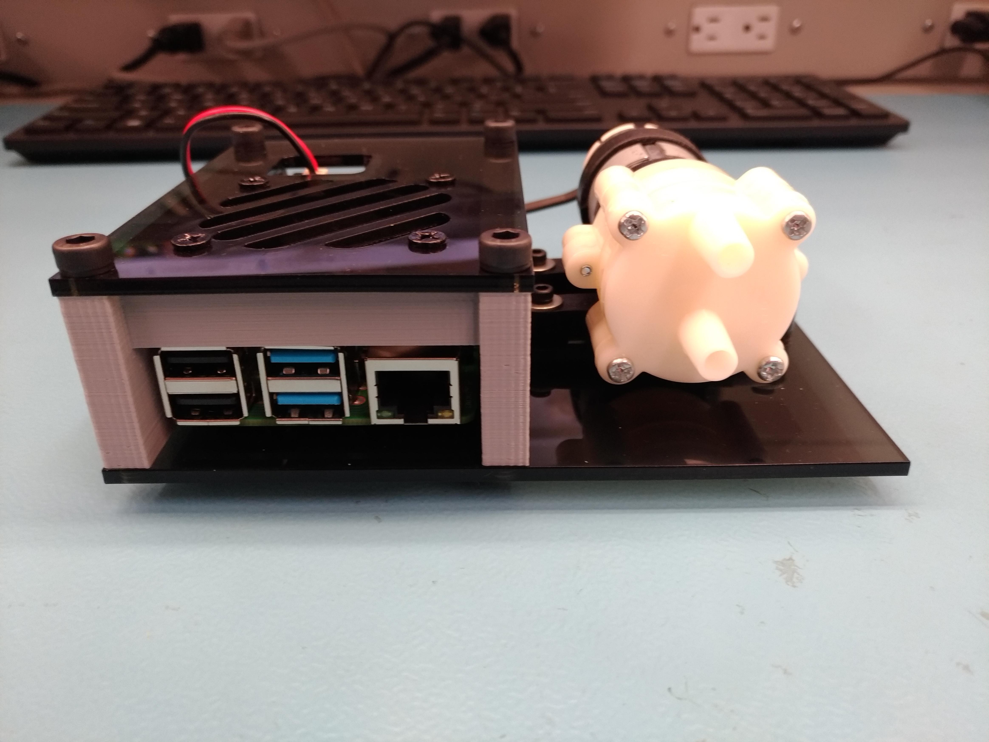
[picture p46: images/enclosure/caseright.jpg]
case4


All measurements/tolerances for this case (3D print parts or laser cut parts) were obtained using a vernier caliper or taken from [this](https://www.raspberrypi.org/documentation/hardware/raspberrypi/mechanical/rpi_MECH_4b_4p0.pdf) Pi 4 blueprint. This case was custom designed by myself.

-----

### November 14, 2019 - Case Parts

I received all my case parts today. The 3D printed middle section, acrylic top/bottom, acrylic washers, and hardware for assembly. I will be stopping by my old workplace to tap the holes on the bottom cover.

The hardware I picked up (no cost):  
(4) M5 x 0.8 x 40mm socket head screw  
(4) M3 x 0.5 x 16mm socket head screw  
(4) M3 x 0.5 nuts  
(4) M2.5 x 0.45 x 10mm button head screw  

Already owned:  
(4) computer case fan screws  
(4) M3 washers  
(4) 3mm thick acrylic washers for under the Pi (so it doesn't rest on its pins)

Pics of individual parts to be posted...

-----

### November 12, 2019 - PCB Power Up

Today during the lab I installed my completed PCB onto the Pi and demonstrated reading sensor values to the professor.  
I also submitted my [week 10 progress report](https://github.com/DBoo92/317Hardware/blob/master/documentation/Week%2010%20Progress%20Report.docx).

Later that day I designed the top and bottom covers for my case. These designs were created in CorelDraw and will be laser cut out of acrylic.

[Top cover:](https://github.com/DBoo92/317Hardware/blob/master/mechanical/CaseTop.pdf) Includes intake slots for the fan and a cutout for the molex connectors.

[Bottom cover:](https://github.com/DBoo92/317Hardware/blob/master/mechanical/CaseBottom.pdf) Motor will be mounted to this as well (beside the Pi).

-----

### November 11, 2019 - Enclosure Design

I designed the middle section of my case which will be enclosed by acrylic plates on the top and bottom. I created this design from scratch using OpenSCAD. This piece has been sent out for 3D printing.

View 1:  
Front cutout - USB and ethernet ports, Side cutout  - USB-C power, HDMI, and audio ports    
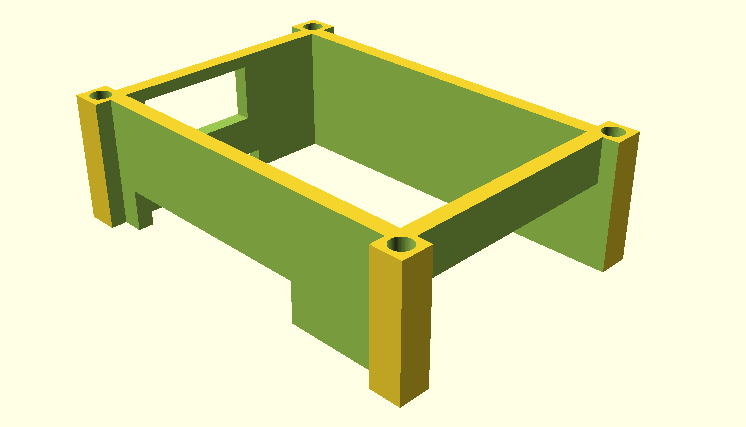
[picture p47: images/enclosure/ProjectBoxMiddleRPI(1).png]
scadfront


View 2:   
Bottom cutout - Pi SD card access, Top cutout - access to switch and DC jack on PCB  
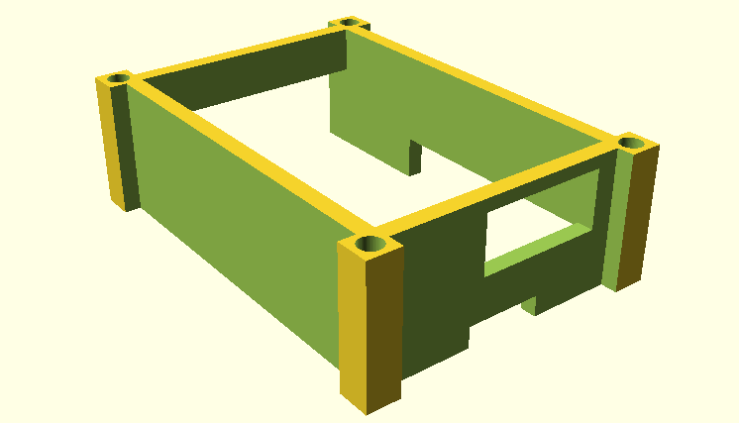
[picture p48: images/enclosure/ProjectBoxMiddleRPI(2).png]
scadback


-----

### November 8, 2019 - Progress Update

Over the weekend I powered up my PCB and got readings from it. I also did some finish wiring/soldering on some components.

PCB power up readings (first 2 columns):   
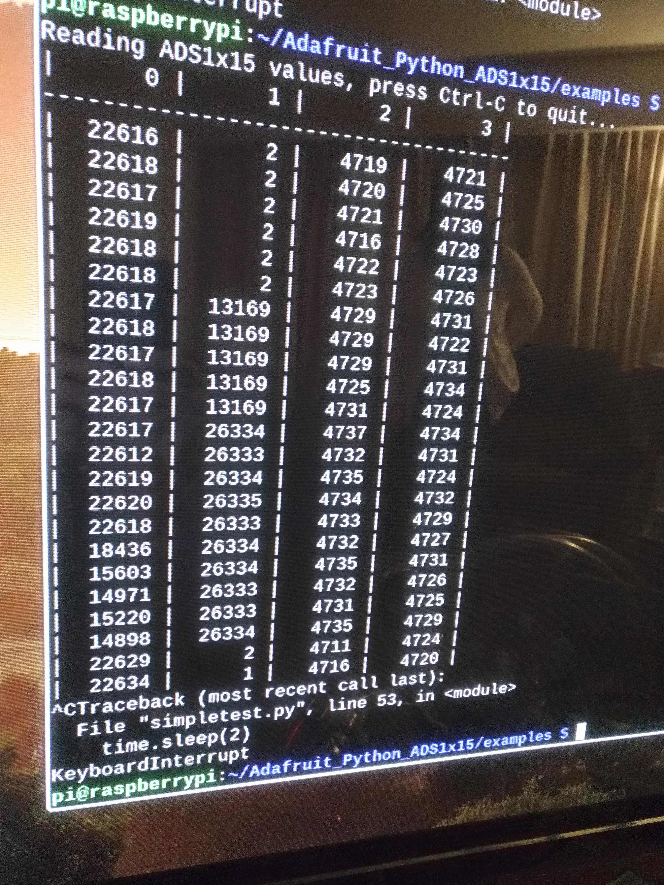
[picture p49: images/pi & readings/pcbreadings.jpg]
pcbread


Extend sensor wires:  
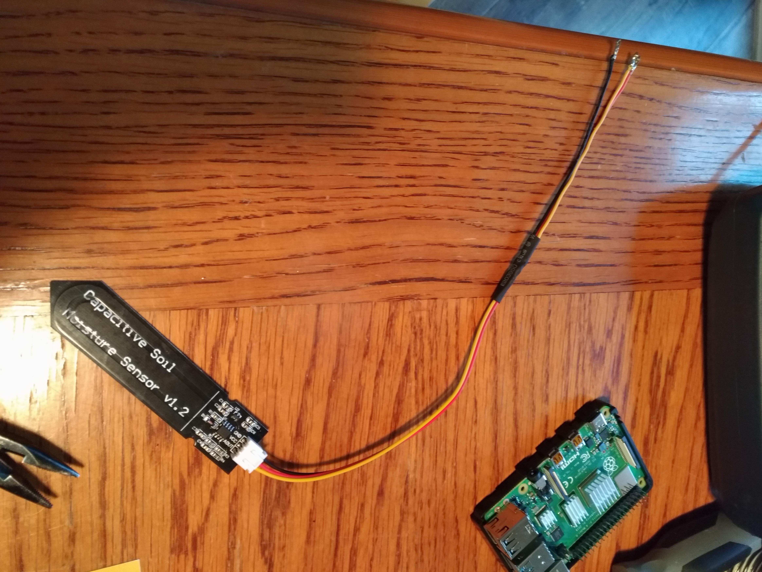
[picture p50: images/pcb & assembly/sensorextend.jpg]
sensextend


Crimp/solder pins for molex connector:    
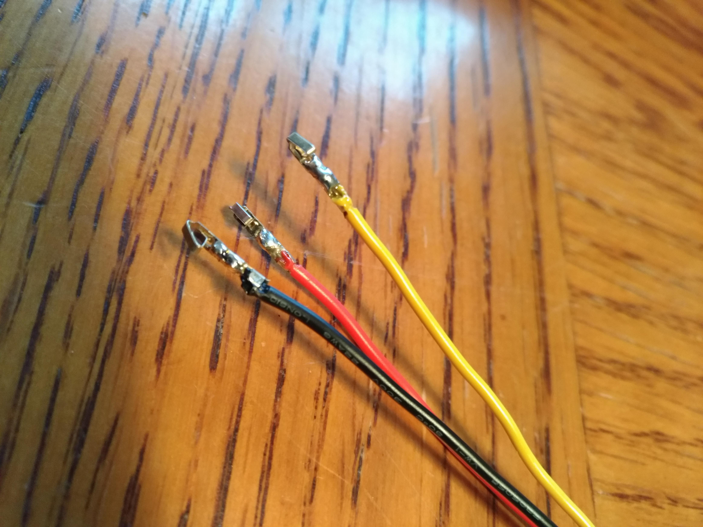
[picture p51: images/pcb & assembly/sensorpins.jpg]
senspins


Soldered a pigtail onto the motor:
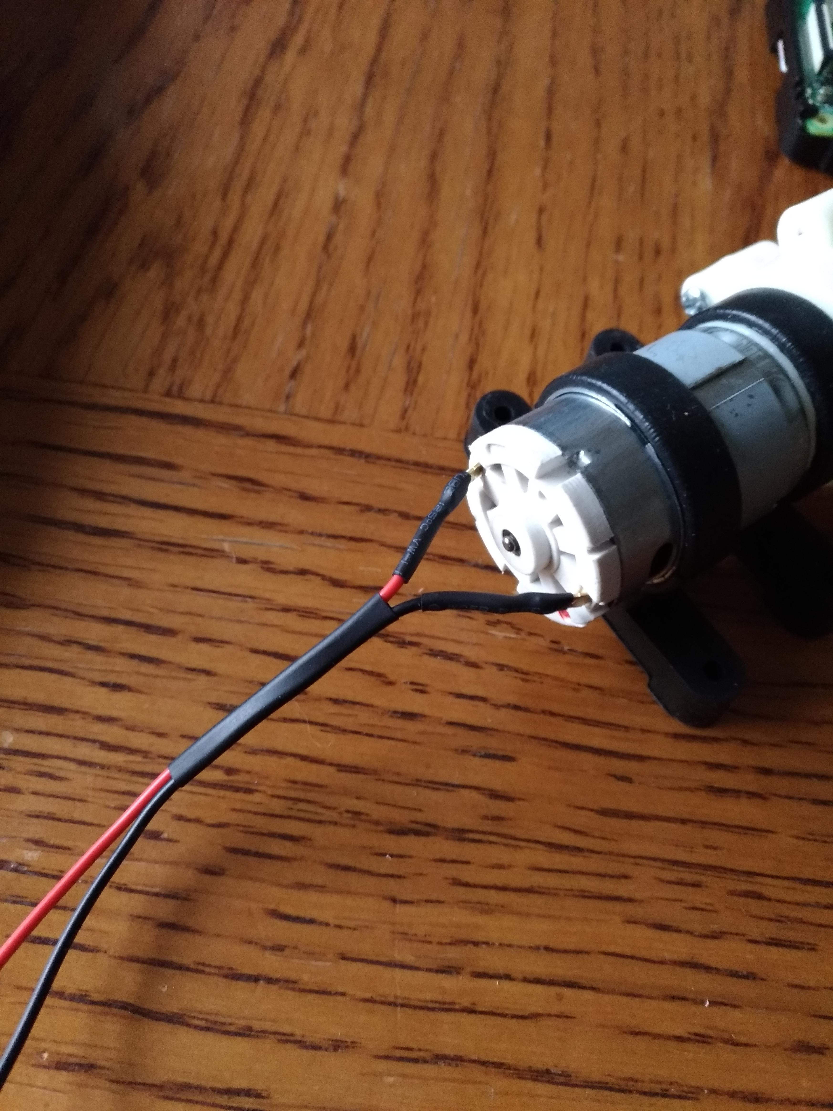
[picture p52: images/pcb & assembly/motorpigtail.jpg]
motorwire


-----

### November 5, 2019 - PCB Soldered

Over the weekend I finished soldering my PCB, here is the result:

Top:   
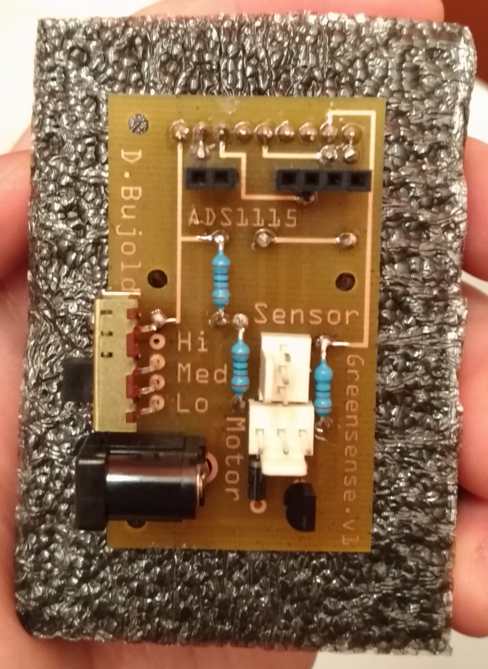
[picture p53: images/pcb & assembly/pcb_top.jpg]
pcbtop


Bottom:  
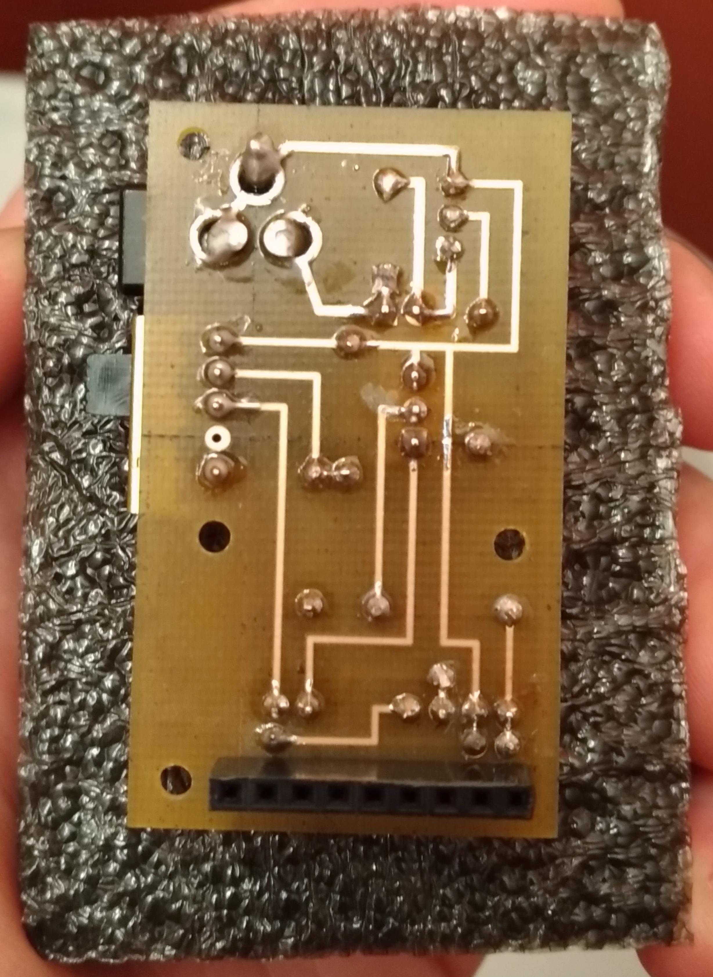
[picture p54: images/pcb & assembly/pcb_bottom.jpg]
pcbbottom


I ran continuity tests on the traces, vias, and between adjacent header pins. Everything passed.
  
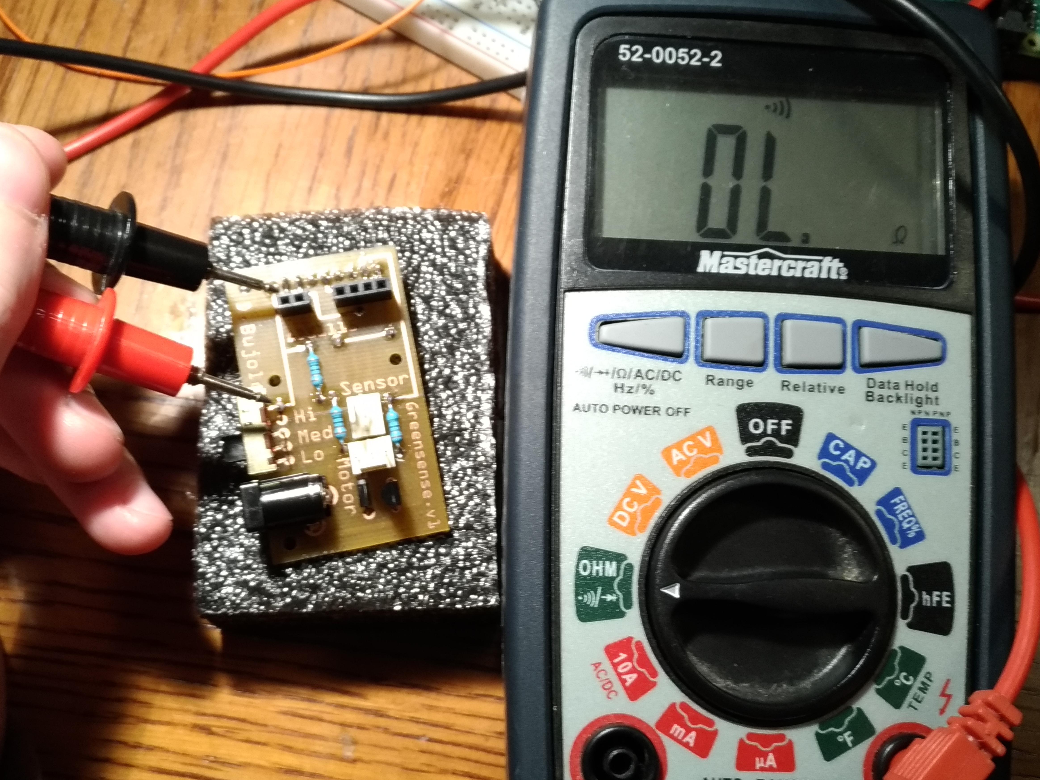
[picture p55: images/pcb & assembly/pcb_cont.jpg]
pcbcont


I tested the fit of the completed PCB onto the Pi using some small risers/washers I had on hand.

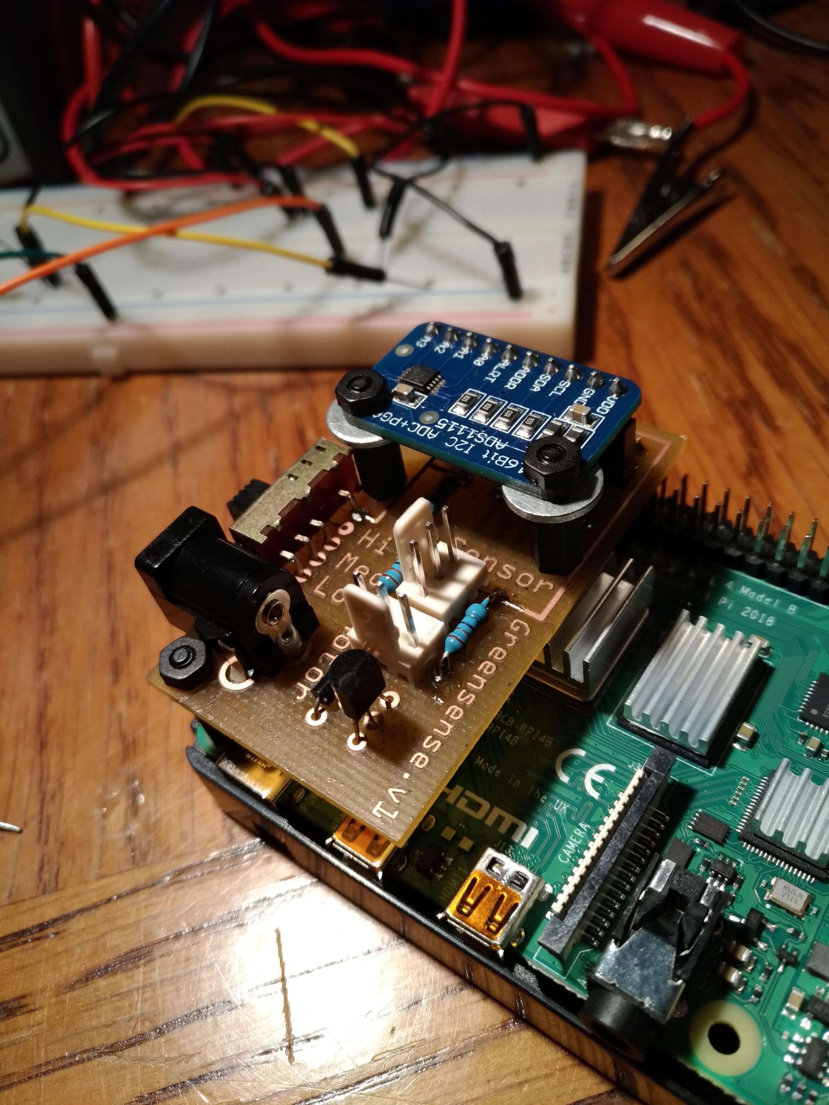
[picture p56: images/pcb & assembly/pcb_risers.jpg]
pcbsetup


I am currently on time with my project schedule.  
My PCB is fully soldered.  
My budget is in the same state as previous weeks (approx. $45 over due to adding ADC and Pi 4 upgrade).  
The system is coming together as planned in my project proposal (with the addition of the watering control switch).

 Next steps:  
 I will be testing the PCB with the Pi/sensor during this week to prepare for the next milestone.  
 Begin the progress report due next week.  
 We are attending the 3D printing seminar on Tuesday as a class.   
 I will begin designing the enclosure following the seminar.

-----

### October 29, 2019 - Breadboarded Milestone

As you can see from my October 14th blog entry, I previously breadboarded all the individual components (unit testing). I will reassemble the full setup (including the ADC and Pi this time) to demonstarte during Tuesday's lab.

Complete Breadboard:  
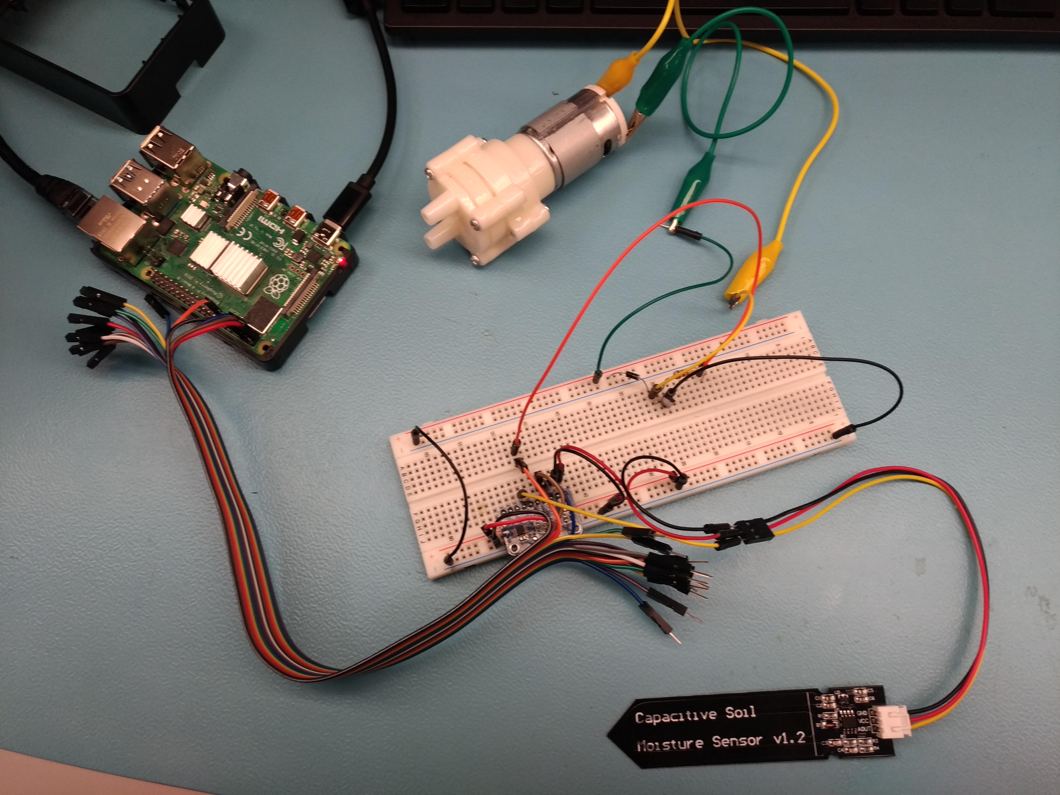
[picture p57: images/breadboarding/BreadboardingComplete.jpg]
Breadboard


I used libraries/sample code from Adafruit to get the analog readings from the ADS1115 and display them, which can be found [here](https://github.com/DBoo92/317Hardware/blob/master/software/simpletest.py).

Initial Readings (soil sensor in far left column):  
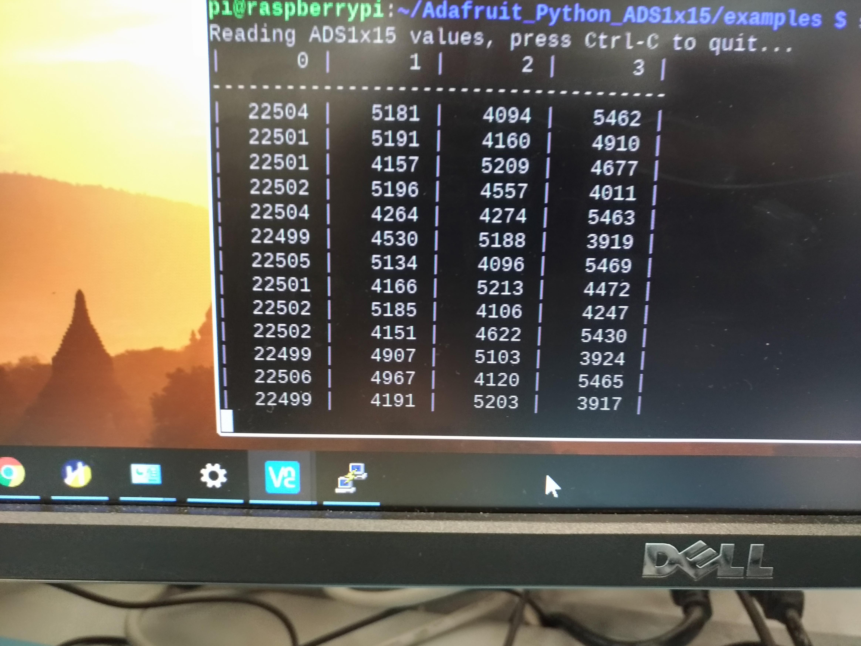
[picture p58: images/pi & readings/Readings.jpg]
Readins1


Change in readings:  
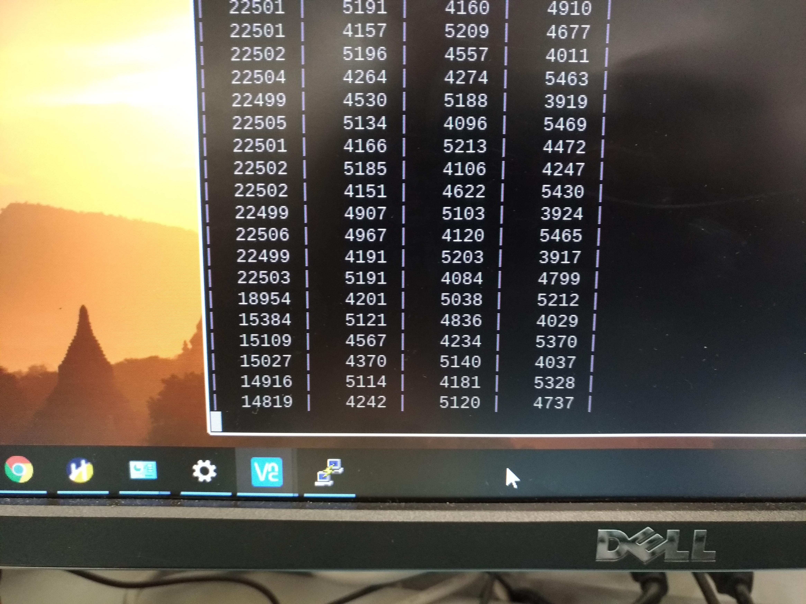
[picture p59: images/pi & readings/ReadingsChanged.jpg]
Readings2


I am currently ahead of my project schedule.  
My breadboarding is complete and I have started soldering. My PCB should be fully soldered in the next few days.  
I am still slightly over budget due to adding the ADC and the Pi 4 upgrade. No extra costs/obstacles since the ADC though.

-----

### October 27, 2019 - Begin Soldering

I picked up my PCB at the beginning of reading week (forgot to take pictures). Here is my current progress on soldering.

ADS1115:  
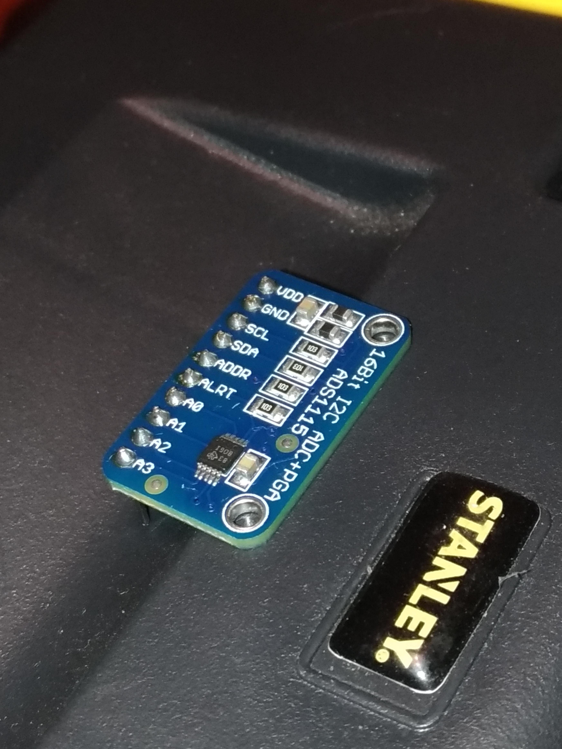
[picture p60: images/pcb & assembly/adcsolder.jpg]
ADC


Vias, Switch, and DC Jack:  
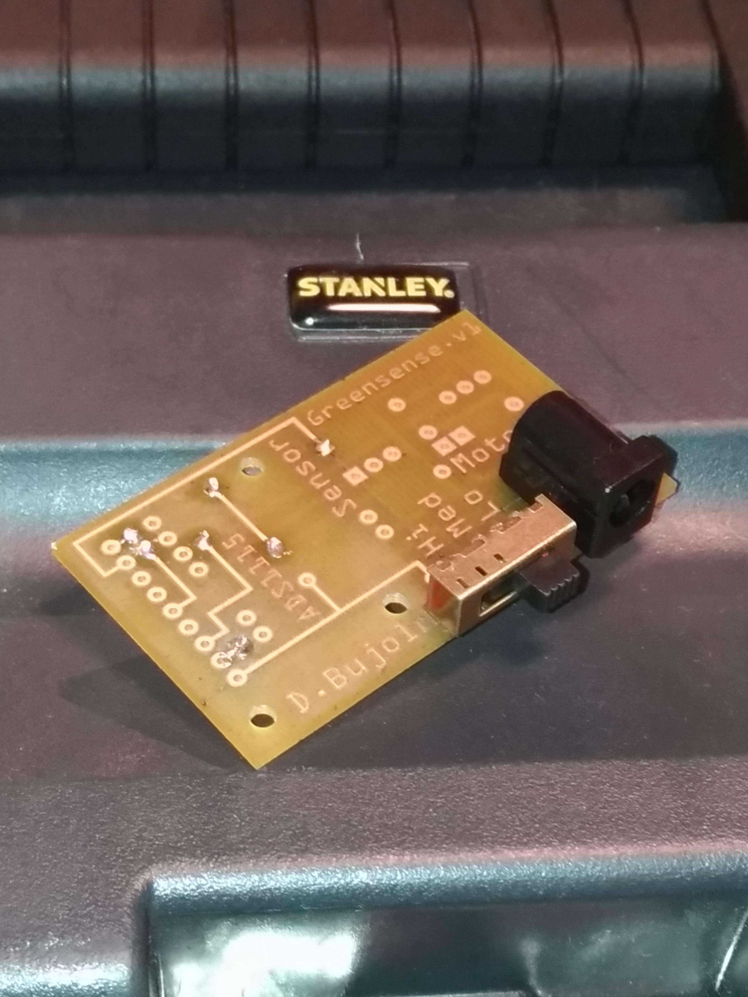
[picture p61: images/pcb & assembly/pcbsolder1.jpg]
PCBtop


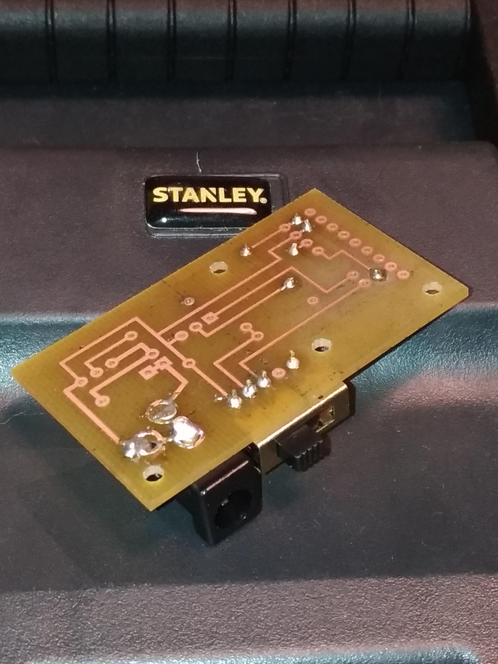
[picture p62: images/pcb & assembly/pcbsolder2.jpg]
PCBbottom


-----

### October 22, 2019 - OS Loaded

During reading week I loaded the Raspbian Buster OS and completed the system configuration.

Powering up:  
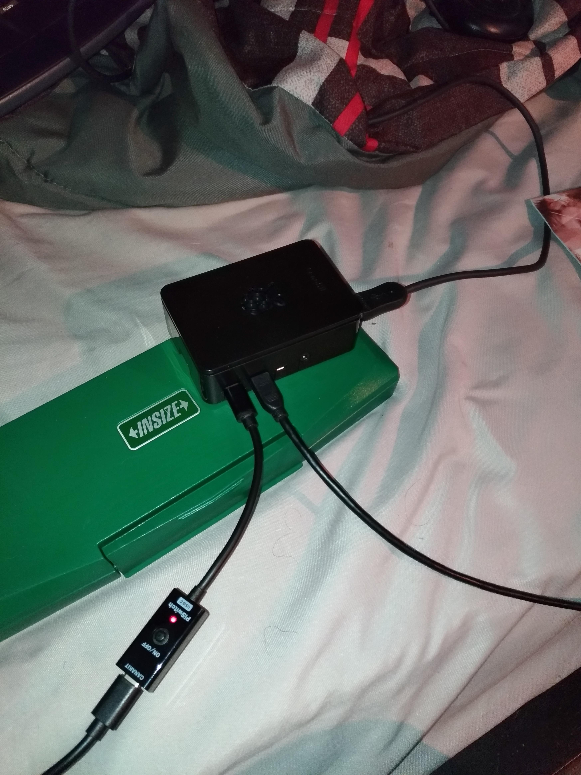
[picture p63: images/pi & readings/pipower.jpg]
PiImage


OS loaded:  
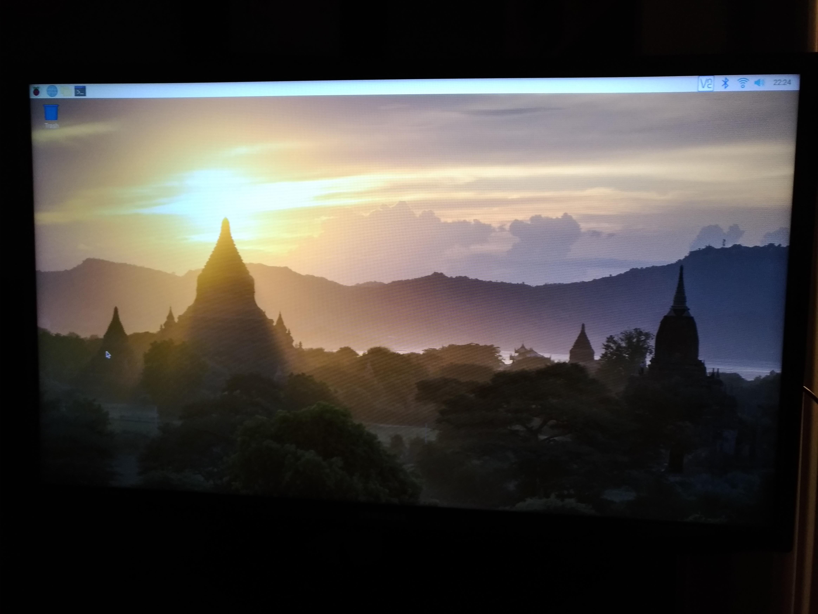
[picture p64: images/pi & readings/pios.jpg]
PiOS


-----

### October 17, 2019 - PCB Update

I moved a few components around and managed to reduce the board width to 33mm (original was 39mm). I also turned the ADS1115 around 180 degrees so I could add mounting holes for it.

I've sent this design in to the prototype lab to be made.

Updated PCB:  
NewPCBImage

-----

### October 15, 2019 - Breadboard and PCB Designed

This weekend I completed my designs using Fritzing. See below...

An SP3T switch is displayed as a 5 pin header (Fritzing didn't have the proper part/none to import).

Kelly recommended using an external power source for the motor (to protect the Pi). I incorporated this by adding a barrel jack for the motor which will connect to a 12v supply.

Breadboard view:
BreadboardImage

Circuit schematic:
SchematicImage

PCB view:  
PCBImage

>I had to create a separate sketch to design the PCB properly (different sketch than breadboard or schematic). Fritzing wouldn't allow me to resize the GPIO header or splice the ADC header (for wire routing). I ended up creating my own headers to make this work.

I am currently ahead of my project schedule.  
My breadboarding is almost complete and my PCB is designed.  
Adding the ADC was a small unforseen obstacle, but I was able to resolve it in a timely and cost effective manner.  
I am currently slightly over budget, approx $8 for the ADC and $35 for the Pi 4 (I considered this a necessary upgrade).  

-----

### October 14, 2019 - Breadboarding Update

Over the last few days I have been testing the individual components of my project by building circuits for them.

Testing the sensor:
SensorTestImage

Readings from the sensor (using Arduino for testing):
SensorReadingsImage

>I had to use an Arduino to test the sensor because I didn't realize the Raspberry Pi has no analog input pins. I will have to add an analog to digital converter to my circuit. I have decided to use the the ADS1115 for its low cost and ease of integration with the Pi. This has been ordered from Amazon (Universal Solder) for $5 + shipping/tax.

Testing the motor:
MotorTestImage

Transistor switching the motor:
MotorCircuitImage

Testing the water control switch:
WaterSwitchImage

I decided to add in this water control switch. It will provide users with selection of 3 different watering levels depending on their plant. This was one of the features Valeria said would be nice to have.

-----

### October 8, 2019 - Show Acquisitions

Image of parts1

Image of parts2

>I realized it will be difficult to use these fan connectors on the PCB as they will require through hole plating. Need to exchange these for breakaway header pins.

Image of parts3

-----

### October 4, 2019 - Parts Pickup

Picked up a GPIO header, and 3 pin fan connectors (male/female) from Sayal Electronics. Picked up a spray nozzle and small fan from Princess Auto today.

My Amazon order also came in the mail today (Pi, sensor, and pump).

-----

### October 1, 2019 - Parts Ordered

The Raspberry Pi 4, capacitive soil sensor, and diaphragm pump have been ordered from Amazon:

Image of order

I will be picking up some of the other components (headers, jumper connectors, spray nozzle, fittings, etc) later this week.

I have decided to choose the Raspberry Pi 4 instead of the 3 B+. Over the last week I have done some research/comparison of the two models. The Pi 4 has a noticeable edge over its predecessor in processing power, memory, GPU performance, microSD card read/write speeds, and networking speed. All of this for a modest price increase. The 4 made more sense for future proofing and long term reusability.

-----

### September 24, 2019 - Budget Due

Click to see the projected [budget](https://github.com/DBoo92/317Hardware/blob/master/documentation/budget/GreenhouseBudget.pdf)

Need to discuss with the professor today whether to use a relay, transistor, or code to turn the effector on/off.

>Kristian has suggested speaking to Kelly or Vlad regarding this.

Decided on the capacitive moisture sensor instead of resistive, due to more accurate readings and corrosion resistance. I have sourced the Gikfun EK1940 from [Amazon](https://www.amazon.ca/gp/product/B07H3P1NRM/ref=ppx_yo_dt_b_asin_title_o00_s00?ie=UTF8&psc=1).

I will also be incorporating a pump/nozzle system to spray water on the soil when moisture readings are low. I will be using the Gikgun EK1856C from [Amazon](https://www.amazon.ca/gp/product/B0744DL1S9/ref=ppx_yo_dt_b_asin_title_o00_s00?ie=UTF8&psc=1).

-----

### September 17, 2019 - Schedule Due

Here you can view the proposed [project schedule pdf](https://github.com/DBoo92/317Hardware/blob/master/documentation/schedule/Project1.pdf).

>Repository edit: Proposal and schedule files moved into nested folders inside Documentation folder.

Met with our project sponsor (Valeria) and received great feedback regarding different features we can implement/how to implement. Meeting report to follow soon.

-----

### September 10, 2019 - Proposal Due

Here you can view the submitted [project proposal pdf](https://github.com/DBoo92/317Hardware/blob/master/documentation/proposal/ProposalContentStudentNameRev03.pdf).

-----

### September 3rd, 2019 - Project Selection

Repository created at 2:42 PM.

Group has been selected. Ryan, Aiden, and Daniel for 317 Hardware and 319 Software.
Selected project is Greenhouse.

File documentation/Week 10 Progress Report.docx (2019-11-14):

Week 10 Progress Report - Capacitive Soil Moisture

CENG 317 – 0NB

Daniel Bujold

November 12, 2019

As the final month of the project approaches I am focusing on completing the last few stages. The last couple weeks have consisted of: soldering parts onto my PCB, verifying the solder job, testing the PCB’s fit on the Raspberry Pi, powering it up for testing, and reading values from the sensor/activating the effector. Soldering went very well. There were no issues or shorts that needed fixing. When I test fit the PCB onto the Pi everything lined up as expected. I was able to find some risers for securing the PCB and analog-to-digital converter. Before the initial power up I double checked all traces, connections, and solder joints. This was to prevent any accidental failures or damage to the Pi. Everything went well during the initial power up. Finally, I tried reading values from my sensor while plugged in to the PCB. Using the same Adafruit sample code from my breadboarded milestone, I was able to pickup sensor values. I then made a simple modification to the program which turns on the motor/water pump when the readings fall outside a certain value. In the first version, I set it to turn the GPIO pin on, but forgot to turn the pin off at program close. This resulted in me having to go back in and change the program code in order to get it to turn off again. But overall, this feature works as well (just needs some fine tuning/coding work). Currently, the project is meeting and exceeding the requirements of the project proposal.

One of the main problems I encountered during this project was the need for an analog-to-digital converter. Originally, I didn’t realize that the Pi was missing analog inputs. I corrected this in a timely and cost effective manner by selecting the ADS1115 as a solution. I sourced this ADC for $5 from Universal Solder on Amazon.ca. Another modification I made was the addition of a DC jack to supply the motor/water pump with power. This came as the suggestion from Kelly Gray in order to isolate the motor from the Pi circuitry and supply if with the proper amount of power. Another issue I just recently encountered was with regards to 3D printing. I designed my .stl file using OpenSCAD and sliced it using Ultimaker Cura. After adjusting the detail and speed settings, Cura was giving me a slice time of 3 – 3.5 hours. The Humber Idea Lab has a printer time limit of 2 hours. I was left with two options: 3D print the case in smaller pieces/sections, or consider other options/materials. Luckily, a coworker offered to 3D print my case on his personal printer (with no time limit). All I had to do was pay for the cost of the filament. I took this opportunity because the filament charge was cheap, and it has the added benefit of 3D printing one solid piece (instead of multiple and having to glue them together).

As with previous reports, I am slightly over project budget. This is due to a few reasons. Firstly, I decided to purchase the Pi 4 instead of the 3B+, which cost $35 more. This was due to the better performance of the 4 and future expandability. Secondly, having to add the ADS1115 set me back another $5. Thirdly, having a case part 3D printed by a friend cost me $5 in printer filament. On the other hand, I recently found some clear acrylic in my supplies at home which saves me around $10. Overall, after factoring in taxes/shipping, I am around $40 over the original proposed budget. I feel like most of the decisions which have incurred extra cost were the right decisions/necessary at the time, and will result in a better final product.

This past week I completed my power up milestone, was able to successfully read my sensor, and manipulate my effector. I designed my 3D printed portion of the case, sliced it, and sent it off to be made. During Tuesday’s lab I will be designing the top and bottom case covers using Corel Draw. Once these designs are complete I will bring them to the prototype lab to be laser cut. As you can see by my current progress, I am on time with my project schedule.

In the coming week I will be testing my case for fitment, tapping the holes in the acrylic, and finish assembling my case. In the weeks following that I will be working on fine tuning the motor/water pump control code, compiling my final presentation in PowerPoint, and creating build instructions for the finished project.

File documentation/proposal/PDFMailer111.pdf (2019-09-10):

43718

Proposal for the development of Greenhouse Health Monitor

Prepared by Daniel Bujold, Ryan McAdie, Aiden Waadallah Computer Engineering Technology Students https://github.com/DBoo92/317Hardware

Executive Summary

As a student in the Computer Engineering Technology program, I will be integrating the knowledge and skills I have learned from our program into this Internet of Things themed capstone project. This proposal requests the approval to build the hardware portion that will connect to a database as well as to a mobile device application. The internet connected hardware will include a custom PCB with the following sensors and actuators BME280 ‐ for temperature and humidity

STEMMA Soil Sensor ‐ for soil moisture level

Solenoid Valve ‐ for dispensing water. The database will store Temperature, humidity, and soil moisture levels from the device. As well as the date/time of each reading and the location of the device (different result sets for different plants/areas).. The mobile device functionality will include The app will allow employees to login, select a desired plant/area, and view those measurements online. It will display the current readings, along with recent min/max readings (all readings time stamped). The user will be able to monitor the health of the greenhouse and even share these results online or through social media. There will be an option to press a button to water the plant if the soil moisture is low. As an added feature, the user will be able to take a picture from the app and share it on social media. and will be further detailed in the mobile application proposal. I will be collaborating with the following company/department I will be collaborating with the Humber Arboretum/nurseries and prof. Kristian Medri on this project.. In the winter semester I plan to form a group with the following students, who are also building similar hardware this term and working on the mobile application with me Daniel Bujold, Ryan McAdie, Aiden Waadallah. The hardware will be completed in CENG 317 Hardware Production Techniques independently and the application will be completed in CENG 319 Software Project. These will be integrated together in the subsequent term in CENG 355 Computer Systems Project as a member of a 2 or 3 student group.

Background

The problem solved by this project is The Humber Arboretum and various other nurseries are lacking a system to monitor temperature, humidity, and soil moisture levels. A system like this would be vital in ensuring the optimal health of the plants. This would allow employees to view and monitor greenhouse conditions in real‐time. Data acquisition will help with adjusting the environment and future planning. This system should theoretically improve plant health, increase yield, decrease resource use, and minimize human error.. A bit of background about this topic is This project solves the need for a measurement/monitoring system in the Humber Arboretum. Such a system will help monitor the health of the plants. Theoretically, this system has the potential to make the greenhouse more effiecient. Existing products on the market include Monnit Greenhouse Monitoring, Sensaphone Greenhouse Remote Monitoring, and Growtronix. I searced through Humber's IEEE subscription and read various articles relating to this topic. The research paper listed below proved to be the most insightful. Having gone through 4 semesters of the Computer Engineering Technology program, I have learned:

‐ Java programming from CENG 212

‐ C programming from CENG 252 and CENG 153

‐ circuit design from CENG 215

‐ application development process in CENG 216

‐ SQL and database from CENG 254 and CENG 256

‐ wireless and connectivity from CENG 253 and CENG 152

These skills sets will enable me to design and build the system required for this project..

Existing products on the market include [1]. I have searched for prior art via Humber’s IEEE subscription selecting “My Subscribed Content”[2] and have found and read [3] which provides insight into similar efforts.

In the Computer Engineering Technology program we have learned about the following topics from the respective relevant courses:

- Java Docs from CENG 212 Programming Techniques In Java,
- Construction of circuits from CENG 215 Digital And Interfacing Systems,
- Rapid application development and Gantt charts from CENG 216 Intro to Software Engineering,
- Micro computing from CENG 252 Embedded Systems,
- SQL from CENG 254 Database With Java,
- Web access of databases from CENG 256 Internet Scripting; and,
- Wireless protocols such as 802.11 from TECH152 Telecom Networks.

This knowledge and skill set will enable me to build the subsystems and integrate them together as my capstone project.

Methodology

This proposal is assigned in the first week of class and is due at the beginning of class in the second week of the fall semester. My coursework will focus on the first two of the 3 phases of this project:
Phase 1 Hardware build.
Phase 2 System integration.
Phase 3 Demonstration to future employers.

Phase 1 Hardware build

The hardware build will be completed in the fall term. It will fit within the CENG Project maximum dimensions of 12 13/16" x 6" x 2 7/8" (32.5cm x 15.25cm x 7.25cm) which represents the space below the tray in the parts kit. The highest AC voltage that will be used is 16Vrms from a wall adaptor from which +/‐ 15V or as high as 45 VDC can be obtained. Maximum power consumption will be 20 Watts.

Phase 2 System integration

The system integration will be completed in the fall term.

Phase 3 Demonstration to future employers

This project will showcase the knowledge and skills that I have learned to potential employers.

The brief description below provides rough effort and non‐labour estimates respectively for each phase. A Gantt chart will be added by week 3 to provide more project schedule details and a more complete budget will be added by week 4. It is important to start tasks as soon as possible to be able to meet deadlines.
We will need to purchase a Raspberry Pi, BME 280 sensor, STEMMA capacitive soil moisture sensor, solenoid valve (rated for liquid), and materials for a device enclosure (for waterproofing/protection).

Concluding remarks

This proposal presents a plan for providing an IoT solution for The solution consists of a Broadcom development platform (Raspberry Pi) connected to various sensors/effectors for monitoring. A BME280 for temperature/humidity, a STEMMA soil moisture sensor, and a solenoid valve for dispensing water. This system can be placed in a specific plant or area in order to take measurements. The device will connect to enterprise WiFi in order to send/receive data. It will store these measurements in a database for analysis. These measurements will be able to be viewed from an app to assist nursery employees. If the soil moisture reading is low, the app will allow the employees to dispense a controlled stream of water into the soil.. This is an opportunity to integrate the knowledge and skills developed in our program to create a collaborative IoT capstone project demonstrating my ability to learn how to support projects such as the initiative described by [3]. I request approval of this project.

References

[1] Monnit Corporation. (n.d.). Greenhouse monitoring.Retrieved from https://www.monnit.com/solutions/greenhouse‐monitoring
[2] Institute of Electrical and Electronics Engineers. (2015, August 28). IEEE Xplore Digital Library [Online]. Available: https://ieeexplore.ieee.org/search/advsearch.jsp
[3] Kumar, A., & Hancke, G. P. (2014). Energy efficient environment monitoring system based on the IEEE 802.15.4 Standard for low cost requirements. IEEE Sensors Journal, 14(8), 2557 ‐ 2566. doi: 10.1109/JSEN.2014.2313348

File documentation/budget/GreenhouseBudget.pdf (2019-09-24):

Parts for 317 Greenhouse Project | 24-Sep-19
Daniel Bujold
Part | Description | Supplier | Part # | CAD$ cost Quantity Shipping Tax | CAD$ subtWebsite | Comments
Raspberry Pi 3 B+ | Includes power supply, SD card | Amazon.ca | B07BCC8PK7 | $98.99 | 1 | $0 | $12.86 | $111.85 | https://www.amazon.ca (https://www.amazon.ca/CanaKit-Raspberry-Starter-Premium-Black/dp/B07BCC8PK7) CanaKit
Soil Moisture Sensor | Capacitive | Amazon.ca | EK1940 | $8.49 | 2 | $0 | $2.20 | $19.18 | https://www.amazon.ca (https://www.amazon.ca/Gikfun-Capacitive-Corrosion-Resistant-Detection/dp/B07H3P1NRM?s=electronics) Gikfun
Mini Diaphragm Pump | Simulate hose/water pressure | Amazon.ca | EK1856C | $11.68 | 1 | $0 | $1.51 | $13.19 | https://www.amazon.ca (https://www.amazon.ca/Gikfun-Aquarium-Cooled-Diaphragm-EK1856C/dp/B0744DL1S9?hvadid=208343092532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) Gikfun
5V relay | Turn pump on/off | Sayal Electronics | 50-530-1 | $3.50 | 1 | $0.45 | $3.95 | | Just an idea. Need to discuss options with Kristian - possible transistor instead?
GPIO Stacking header | To connect PCB to RPI | Sayal Electronics | ? | $4.75 | 1 | $0.61 | $5.36 | | Can't find online, but verified in stock
Pin/socket connectors | Connect wires to PCB and sensor | Sayal Electronics | ? | $0.82 | 4 | $0.42 | $3.70 | | Can't find online, but verified in stock
Sayal Electronics pickup | $0.58 x kilometers | | | | 20 | | $11.60 | https://www.canada.ca/ | Canada.ca per kilometer allowance for employees/employers
Cone spray nozzle | To spray water evenly | Princess Auto | 8116626 | $5.97 | 1 | $0.77 | $6.74 | https://www.princessau (https://www.princessauto.com/en/detail/-18-adjustable-brass-spray-nozzle/A-p8116626e) .
Barbed NPT fitting | To connect sprayer to clear tube | Princess Auto | ? | $3.50 | 1 | $0.45 | $3.95 | | Need to find exact size of sprayer threads
Princess Auto pickup | $0.58 x kilometers | | | | 0 | | $0 | | Included in Sayal pickup (its on the way)
PCB | Connect sensor/effector with RPI | Prototype Lab | 1 | $0 | Use prototype lab to save expense
Clear acrylic 24" x 12" | For project enclosure | Laird Plastics | 3/16" | $8.20 | 1 | $1.06 | $9.26 | Phone quote
Acrylic cutting | | Prototype Lab | | | 1 | | $0 | Prototype Lab or cut it myself on table saw

Already Owned

Acrylic glue | To assemble acrylic panels | 1 | $0 | 50 mL bottle
Solder | To solder wires/PCB | 1 | $0 | Roll
Various resistors | Selection in coming weeks* | | $0 | various resistors from different parts kits
Various diodes/transistors | Selection in coming weeks* | | $0 | various components from different parts kits
Assorted screws, nuts, bolts | | | $0 | various hardware collected in my toolbox
Electrical wire | 18-22 AWG | | $0 | approx 8' needed
Heatshrink tube 2:1 | To cover wires/connections | | $0 | various sizes collected in my toolbox
Clear PVC tube | To plumb water system | | $0 | approx 3' needed
Zip ties | Securing wires | | $0 | 6" zip ties

Totals

$CAD Grand Total | $188.78


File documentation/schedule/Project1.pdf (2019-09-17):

1 | Select group and project | 2 hrs | Tue 9/3/19 | Tue 9/3/19
2 | Research IEEE papers | 1 hr | Thu 9/5/19 | Thu 9/5/19 | 1

Task Name; DurationStart; Finish; PredecessorsResource Names; Find existing products/solutions 0.5 hrs Thu 9/5/19; Thu 9/5/19; Brainstorm project ideas,; research sensors; 1 day; Fri 9/6/19; Create proposal; Sun 9/8/19; Proposal due; 0 hrs; Tue 9/10/19 Tue 9/10/19; Start project schedule; 4 days; Tue 9/10/19 Fri 9/13/19; Project schedule due; 0 days; Tue 9/17/19 Tue 9/17/19; Kick off meeting; Create budget/search products; 3 days; Tue 9/17/19 Thu 9/19/19; Budget due; Tue 9/24/19 Tue 9/24/19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

Manual Summary Rollup

ID | Task Name | DurationStart | Finish | PredecessorsResource Names
17 | Assemble/test breadboard | 4 days | Tue
10/15/19
Fri 10/18/19 | 16
18 | Reading week (light work on

## PCB/breadboard)

## 5 days Mon

10/21/19

## Fri 10/25/19

19 | Breadboard assembled | 0 days | Tue
10/29/19

## Tue

10/29/19

16,17

20 | Solder/finish PCB | 5 days | Mon 10/28/19Fri 11/1/19 | 16
21 | PCB soldered | 0 days | Tue 11/5/19 Tue 11/5/19 | 16,19
22 | Test PCB/fix issues | 5 days | Mon 11/4/19Fri 11/8/19
23 | PCB power up test | 0 days | Tue 11/12/19Tue 11/12/19 21
24 | Design/build enclosure | 5 days | Mon
11/4/19
Fri 11/8/19 | 12,16
25 | Project enclosure due | 0 days | Tue
11/19/19

## Tue

11/19/19

24

26 | Work on final presentation | 7 days | Thu
11/14/19
Fri 11/22/19 | 19,21,23,24
27 | Presentation due (be ready to

## present)

## 0 days Mon

11/25/19

## Mon

11/25/19

26

28 | Presentations (2nd week) | 2 hrs | Tue 12/3/19 Tue 12/3/19
29 | Create final build instructions | 8 days | Wed
11/27/19
Fri 12/6/19 | 19,21,24
30 | Build instructions due | 0 days | Tue
12/10/19

## Tue

12/10/19

29

2 | 4 | 6 | 8 | 10 | 12 | 14 | 16 | 18 | 20

September 2019

Task; Split; Milestone; Summary; Project Summary; Inactive Task; Inactive Summary; Manual Task; Duration-only; Manual Summary Rollup; Manual Summary; Start-only; External Tasks; External Milestone; Deadline; Progress; Manual Progress; Project: Project1.mpp Date: Tue 9/17/19

ID | Task Name | DurationStart | Finish | PredecessorsResource Names
31 | Meet with client to review

## progress

## 1 hr Wed

12/11/19

## Wed

12/11/19

27

## 32 Post semester meeting (review semester/discuss future)

## 2 hrs Fri

12/13/19

| | | Fri 12/13/19 | 31
33 | Winter break | 17 days

## Sat

12/14/19

## Sun 1/5/20

34 | Pre semester meeting (discuss
new ideas/begin planning for 355) steps/developments | 2 hrs 1 hr | Thu 1/2/20 Tue 1/7/20 | Thu 1/2/20 Tue 1/7/20 | 32 35
times once semester 6 starts software requirements specification | 4 days 0 days | Wed 1/8/20 Mon 1/13/20 35,36 1/13/20 Mon 1/20/20 | Mon 1/13/20 Mon 1/20/20
35 | Scheduling and group meeting | 2 hrs | Mon 1/6/20 | Mon 1/6/20 | 34
36 | Meet with client to discuss next
37 | Revise schedule and add task
38 | Group project status update | 0 days | Mon
39 | App, web, and database
40 | Group project status update | 0 days | Mon 1/27/20 | Mon 1/27/20
41 | Group project status update | 0 days | Mon 2/3/20 | Mon 2/3/20
2 | 4 | 6 | 8 | 10 | 12 | 14 | 16 | 18 | 20

September 2019

ID | Task Name | DurationStart | Finish | PredecessorsResource Names
42 | App, web, and database

## independent demonstration

## 0 days Mon

2/10/20

## Mon 2/10/20

43 | Group project status update | 0 days | Mon
2/17/20

## Mon 2/17/20

44 | Reading week | 5 days | Mon
2/24/20

## Fri 2/28/20

45 | Group integration | 0 days | Mon 3/2/20 | Mon 3/2/20
46 | Group project status update | 0 days | Mon 3/9/20 | Mon 3/9/20
47 | Group troubleshooting | 0 days | Mon
3/16/20

## Mon 3/16/20

48 | Group project status update | 0 days | Mon
3/23/20

## Mon 3/23/20

## 49 Group physical enclosure complete

## 0 days Mon

3/30/20

## Mon 3/30/20

50 | Project demonstration | 0 days | Mon 4/6/20 | Mon 4/6/20
51 | Final presentation due | 0 days | Mon
4/13/20

## Mon 4/13/20

## 52 Final report due (15th week on critical path, but last day of classes is the 17th??)

## 0 days Mon

4/20/20

## Mon 4/20/20

2 | 4 | 6 | 8 | 10 | 12 | 14 | 16 | 18 | 20

September 2019

October 2019; November 2019; Task; Split; Milestone; Summary; Project Summary; Inactive Task; Inactive Summary; Manual Task; Duration-only; Manual Summary; Start-only; External Tasks; External Milestone; Deadline; Progress; Manual Progress; Project: Project1.mpp Date: Tue 9/17/19

Manual Summary Rollup

10/29

11/5

October 2019; November 2019; Task; Split; Milestone; Summary; Project Summary; Inactive Task; Inactive Summary; Manual Task; Duration-only; Manual Summary; Start-only; External Tasks; External Milestone; Deadline; Progress; Manual Progress; Project: Project1.mpp Date: Tue 9/17/19

Manual Summary Rollup

20 | 22 | 24 | 26 | 28 | 30 | 2 | 4 | 6 | 8 | 10 | 12 | 14 | 16 | 18 | 20 | 22 | 24 | 26 | 28 | 30 | 1 | 3 | 5 | 7 | 9 | 11
October 2019 | November 2019

20 | 22 | 24 | 26 | 28 | 30 | 2 | 4 | 6 | 8 | 10 | 12 | 14 | 16 | 18 | 20 | 22 | 24 | 26 | 28 | 30 | 1 | 3 | 5 | 7 | 9 | 11
October 2019 | November 2019

13 | 15 | 17 | 19 | 21 | 23 | 25 | 27 | 29 | 1 | 3 | 5 | 7 | 9 | 11 | 13 | 15 | 17 | 19 | 21 | 23 | 25 | 27 | 29 | 31 | 2 | 4
December 2019 | January 2020

December 2019; January 2020; Task; Split; Milestone; Summary; Project Summary; Inactive Task; Inactive Summary; Manual Task; Duration-only; Manual Summary; Start-only; External Tasks; External Milestone; Deadline; Progress; Manual Progress; Project: Project1.mpp Date: Tue 9/17/19

Manual Summary Rollup

December 2019; January 2020; Task; Split; Milestone; Summary; Project Summary; Inactive Task; Inactive Summary; Manual Task; Duration-only; Manual Summary Rollup; Manual Summary; Start-only; External Tasks; External Milestone; Deadline; Progress; Manual Progress; Project: Project1.mpp Date: Tue 9/17/19

13 | 15 | 17 | 19 | 21 | 23 | 25 | 27 | 29 | 1 | 3 | 5 | 7 | 9 | 11 | 13 | 15 | 17 | 19 | 21 | 23 | 25 | 27 | 29 | 31 | 2 | 4
December 2019 | January 2020

6 | 8 | 10 | 12 | 14 | 16 | 18 | 20 | 22 | 24 | 26 | 28 | 30 | 1 | 3 | 5 | 7 | 9 | 11 | 13 | 15 | 17 | 19 | 21 | 23 | 25 | 27
January 2020 | February 2020

6 | 8 | 10 | 12 | 14 | 16 | 18 | 20 | 22 | 24 | 26 | 28 | 30 | 1 | 3 | 5 | 7 | 9 | 11 | 13 | 15 | 17 | 19 | 21 | 23 | 25 | 27
January 2020 | February 2020

January 2020; February 2020; Task; Split; Milestone; Summary; Project Summary; Inactive Task; Inactive Summary; Manual Task; Duration-only; Manual Summary Rollup; Manual Summary; Start-only; External Tasks; External Milestone; Deadline; Progress; Manual Progress; Project: Project1.mpp Date: Tue 9/17/19

January 2020; February 2020

29 | 2 | 4 | 6 | 8 | 10 | 12 | 14 | 16 | 18 | 20 | 22 | 24 | 26 | 28 | 30 | 1 | 3 | 5 | 7 | 9 | 11 | 13 | 15 | 17 | 19 | 21
March 2020 | April 2020

29 | 2 | 4 | 6 | 8 | 10 | 12 | 14 | 16 | 18 | 20 | 22 | 24 | 26 | 28 | 30 | 1 | 3 | 5 | 7 | 9 | 11 | 13 | 15 | 17 | 19 | 21
March 2020 | April 2020

29 | 2 | 4 | 6 | 8 | 10 | 12 | 14 | 16 | 18 | 20 | 22 | 24 | 26 | 28 | 30 | 1 | 3 | 5 | 7 | 9 | 11 | 13 | 15 | 17 | 19 | 21
March 2020 | April 2020

3/2

March 2020; April 2020; Task; Split; Milestone; Summary; Project Summary; Inactive Task; Inactive Summary; Manual Task; Duration-only; Manual Summary; Start-only; External Tasks; External Milestone; Deadline; Progress; Manual Progress; Project: Project1.mpp Date: Tue 9/17/19

Manual Summary Rollup

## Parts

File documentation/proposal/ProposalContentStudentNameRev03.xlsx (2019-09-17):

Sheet: DataEntry
CENG 317 Proposal | Daniel Bujold (N01241627)
Submission Date | 2019-09-10
Project Name | Greenhouse Health Monitor
Student Names | Daniel Bujold, Ryan McAdie, Aiden Waadallah
Project repository | https://github.com/DBoo92/317Hardware
SensorsEffectors choices | BME280 - for temperature and humidity STEMMA Soil Sensor - for soil moisture level Solenoid Valve - for dispensing water
The database will store | Temperature, humidity, and soil moisture levels from the device. As well as the date/time of each reading and the location of the device (different result sets for different plants/areas).
The mobile device functionality will include | The app will allow employees to login, select a desired plant/area, and view those measurements online. It will display the current readings, along with recent min/max readings (all readings time stamped). The user will be able to monitor the health of the greenhouse and even share these results online or through social media. There will be an option to press a button to water the plant if the soil moisture is low. As an added feature, the user will be able to take a picture from the app and share it on social media.
I will be collaborating with the following company/department | I will be collaborating with the Humber Arboretum/nurseries and prof. Kristian Medri on this project.
My group in the winter semester will include | Daniel Bujold, Ryan McAdie, Aiden Waadallah
50 word problem statement | The Humber Arboretum and various other nurseries are lacking a system to monitor temperature, humidity, and soil moisture levels. A system like this would be vital in ensuring the optimal health of the plants. This would allow employees to view and monitor greenhouse conditions in real-time. Data acquisition will help with adjusting the environment and future planning. This system should theoretically improve plant health, increase yield, decrease resource use, and minimize human error.
100 words of background | This project solves the need for a measurement/monitoring system in the Humber Arboretum. Such a system will help monitor the health of the plants. Theoretically, this system has the potential to make the greenhouse more effiecient. Existing products on the market include Monnit Greenhouse Monitoring, Sensaphone Greenhouse Remote Monitoring, and Growtronix. I searced through Humber's IEEE subscription and read various articles relating to this topic. The research paper listed below proved to be the most insightful. Having gone through 4 semesters of the Computer Engineering Technology program, I have learned: - Java programming from CENG 212 - C programming from CENG 252 and CENG 153 - circuit design from CENG 215 - application development process in CENG 216 - SQL and database from CENG 254 and CENG 256 - wireless and connectivity from CENG 253 and CENG 152 These skills sets will enable me to design and build the system required for this project.
Current product APA citation | Monnit Corporation. (n.d.). Greenhouse monitoring.Retrieved from https://www.monnit.com/solutions/greenhouse-monitoring
Existing research IEEE paper APA citation | Kumar, A., & Hancke, G. P. (2014). Energy efficient environment monitoring system based on the IEEE 802.15.4 Standard for low cost requirements. IEEE Sensors Journal, 14(8), 2557 - 2566. doi: 10.1109/JSEN.2014.2313348
Brief description of planned purchases | We will need to purchase a Raspberry Pi, BME 280 sensor, STEMMA capacitive soil moisture sensor, solenoid valve (rated for liquid), and materials for a device enclosure (for waterproofing/protection).
Solution description | The solution consists of a Broadcom development platform (Raspberry Pi) connected to various sensors/effectors for monitoring. A BME280 for temperature/humidity, a STEMMA soil moisture sensor, and a solenoid valve for dispensing water. This system can be placed in a specific plant or area in order to take measurements. The device will connect to enterprise WiFi in order to send/receive data. It will store these measurements in a database for analysis. These measurements will be able to be viewed from an app to assist nursery employees. If the soil moisture reading is low, the app will allow the employees to dispense a controlled stream of water into the soil.

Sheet: DataBase
Submission Date | Project Name | Student Names | Project repository | SensorsEffectors choices | The database will store | The mobile device functionality will include | I will be collaborating with the following company/department | My group in the winter semester will include | 50 word problem statement | 100 words of background | Current product APA citation | Existing research IEEE paper APA citation | Brief description of planned purchases | Solution description
43718 | Greenhouse Health Monitor | Daniel Bujold, Ryan McAdie, Aiden Waadallah | https://github.com/DBoo92/317Hardware | BME280 - for temperature and humidity STEMMA Soil Sensor - for soil moisture level Solenoid Valve - for dispensing water | Temperature, humidity, and soil moisture levels from the device. As well as the date/time of each reading and the location of the device (different result sets for different plants/areas). | The app will allow employees to login, select a desired plant/area, and view those measurements online. It will display the current readings, along with recent min/max readings (all readings time stamped). The user will be able to monitor the health of the greenhouse and even share these results online or through social media. There will be an option to press a button to water the plant if the soil moisture is low. As an added feature, the user will be able to take a picture from the app and share it on social media. | I will be collaborating with the Humber Arboretum/nurseries and prof. Kristian Medri on this project. | Daniel Bujold, Ryan McAdie, Aiden Waadallah | The Humber Arboretum and various other nurseries are lacking a system to monitor temperature, humidity, and soil moisture levels. A system like this would be vital in ensuring the optimal health of the plants. This would allow employees to view and monitor greenhouse conditions in real-time. Data acquisition will help with adjusting the environment and future planning. This system should theoretically improve plant health, increase yield, decrease resource use, and minimize human error. | This project solves the need for a measurement/monitoring system in the Humber Arboretum. Such a system will help monitor the health of the plants. Theoretically, this system has the potential to make the greenhouse more effiecient. Existing products on the market include Monnit Greenhouse Monitoring, Sensaphone Greenhouse Remote Monitoring, and Growtronix. I searced through Humber's IEEE subscription and read various articles relating to this topic. The research paper listed below proved to be the most insightful. Having gone through 4 semesters of the Computer Engineering Technology program, I have learned: - Java programming from CENG 212 - C programming from CENG 252 and CENG 153 - circuit design from CENG 215 - application development process in CENG 216 - SQL and database from CENG 254 and CENG 256 - wireless and connectivity from CENG 253 and CENG 152 These skills sets will enable me to design and build the system required for this project. | Monnit Corporation. (n.d.). Greenhouse monitoring.Retrieved from https://www.monnit.com/solutions/greenhouse-monitoring | Kumar, A., & Hancke, G. P. (2014). Energy efficient environment monitoring system based on the IEEE 802.15.4 Standard for low cost requirements. IEEE Sensors Journal, 14(8), 2557 - 2566. doi: 10.1109/JSEN.2014.2313348 | We will need to purchase a Raspberry Pi, BME 280 sensor, STEMMA capacitive soil moisture sensor, solenoid valve (rated for liquid), and materials for a device enclosure (for waterproofing/protection). | The solution consists of a Broadcom development platform (Raspberry Pi) connected to various sensors/effectors for monitoring. A BME280 for temperature/humidity, a STEMMA soil moisture sensor, and a solenoid valve for dispensing water. This system can be placed in a specific plant or area in order to take measurements. The device will connect to enterprise WiFi in order to send/receive data. It will store these measurements in a database for analysis. These measurements will be able to be viewed from an app to assist nursery employees. If the soil moisture reading is low, the app will allow the employees to dispense a controlled stream of water into the soil.

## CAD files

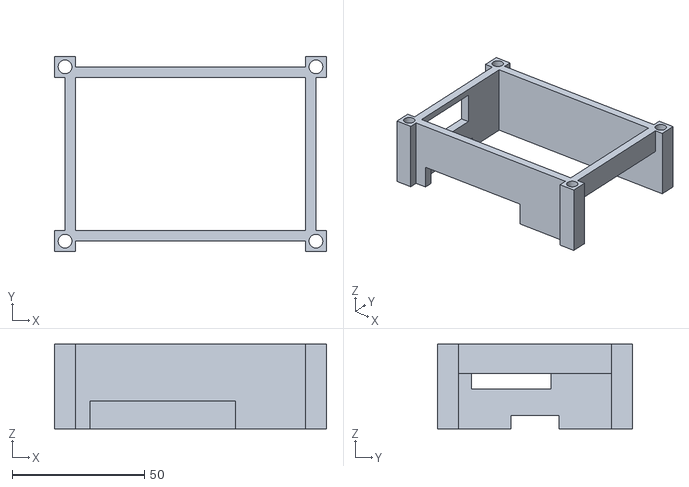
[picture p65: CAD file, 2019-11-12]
mechanical/ProjectBoxMiddleRPI.stl
103.0 x 74.0 x 32.0

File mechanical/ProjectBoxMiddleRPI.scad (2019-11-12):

$fn=64;
difference(){
    //main cube
    {
        xdim2 = 103;
        ydim2 = 74;
        zdim2 = 32;
        translate([-xdim2/2, -ydim2/2, -zdim2])
        {
            cube([xdim2,ydim2,zdim2]);
        }
    }
    
    xdim1 = 87;
    ydim1 = 58;
    zdim1 = 32;
    //center cut out
    translate([-xdim1/2, -ydim1/2, -zdim1])
    {
        cube([xdim1,ydim1,zdim1]);
    }
    //long side 1 indent
    translate([-xdim1/2, -37, -zdim1])
    {
        cube([xdim1,4,zdim1]);
    }
    //long side 2 indent
    translate([-xdim1/2, 33, -zdim1])
    {
        cube([xdim1,4,zdim1]);
    }
    //short side 1 indent
    translate([-51.5, -ydim1/2, -zdim1])
    {
        cube([4,ydim1,zdim1]);
    }
    //short side 2 indent
    translate([47.5, -ydim1/2, -zdim1])
    {
        cube([4,ydim1,zdim1]);
    }
    //cutout for usb and eth
    translate([43.5, -ydim1/2, -zdim1])
    {
        cube([4,ydim1,21]);
    }
    //cutout for sd card
    translate([-47.5, -9, -zdim1])
    {
        cube([4,18,5]);
    }
    //cutout for switch
    translate([-47.5, -24, -17])
    {
        cube([4,30,14]);
    }
    //cutout for video/audio
    translate([-38, -33, -zdim1])
    {
        cube([55,4,10.5]);
    }
    
    radius = 2.6;
    //hole in Q4
    translate([-47.5,33,-zdim1])
    {
        cylinder (zdim1,radius,radius);
    }
    //hole in Q3
    translate([-47.5,-33,-zdim1])
    {
        cylinder (zdim1,radius,radius);
    }
    //hole in Q2
    translate([47.5,-33,-zdim1])
    {
        cylinder (zdim1,radius,radius);
    }
    //hole in Q1
    translate([47.5,33,-zdim1])
    {
        cylinder (zdim1,radius,radius);
    }
    
}

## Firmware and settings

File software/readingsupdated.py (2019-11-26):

# readingsupdated.py
# Read analog values from ADS1115 for soil moisture and output GPIO pin to turn on motor
# Author: Tony DiCola (modified by Daniel Bujold)
# License: Public Domain

import time
import RPi.GPIO as GPIO
GPIO.setmode(GPIO.BCM)
GPIO.setwarnings(False)
GPIO.setup(22,GPIO.OUT)

# Import the ADS1x15 module.
import Adafruit_ADS1x15

# Create an ADS1115 ADC (16-bit) instance.
adc = Adafruit_ADS1x15.ADS1115()

# Note you can change the I2C address from its default (0x48), and/or the I2C
# bus by passing in these optional parameters:
#adc = Adafruit_ADS1x15.ADS1015(address=0x49, busnum=1)

# Choose a gain of 1 for reading voltages from 0 to 4.09V.
# Or pick a different gain to change the range of voltages that are read:
#  - 2/3 = +/-6.144V
#  -   1 = +/-4.096V
#  -   2 = +/-2.048V
#  -   4 = +/-1.024V
#  -   8 = +/-0.512V
#  -  16 = +/-0.256V
# See table 3 in the ADS1015/ADS1115 datasheet for more info on gain.
GAIN = 1

print('Reading ADS1x15 values, press Ctrl-C to quit...')
# Print nice channel column headers.
print('| {0:>6} | {1:>6} | {2:>6} | {3:>6} |'.format(*range(4)))
print('-' * 37)
# Main loop.
while True:
    # Read all the ADC channel values in a list.
    values = [0]*4
    for i in range(4):
        # Read the specified ADC channel using the previously set gain value.
        values[i] = adc.read_adc(i, gain=GAIN)
        # Note you can also pass in an optional data_rate parameter that controls
        # the ADC conversion time (in samples/second). Each chip has a different
        # set of allowed data rate values, see datasheet Table 9 config register
        # DR bit values.
        #values[i] = adc.read_adc(i, gain=GAIN, data_rate=128)
        # Each value will be a 12 or 16 bit signed integer value depending on the
        # ADC (ADS1015 = 12-bit, ADS1115 = 16-bit).
    # Print the ADC values.
    print('| {0:>6} | {1:>6} | {2:>6} | {3:>6} |'.format(*values))

    # Declare variable for watering level switch
    water_lvl = 0

    # Declare variable for moisture reference value
    ref = 13000

    # Set watering level
    if (values[1] < 1000):
	water_lvl = 0.5
    elif (values[1] > 12000 and values[1] < 14000):
	water_lvl = 1.5
    elif (values[1] > 24000):
	water_lvl = 3
    else:
	water_lvl = 1

    # Turn on motor/watering system if soil moisture is too low
    if (values[0] > ref):
        GPIO.output(22,GPIO.HIGH)
        # Turn motor on for water_lvl seconds
	   time.sleep(water_lvl)
        GPIO.output(22,GPIO.LOW)
        # sleep to allow water absorbtion before recheck
	   time.sleep(10)

    # Pause for 2 seconds.
    time.sleep(2)
